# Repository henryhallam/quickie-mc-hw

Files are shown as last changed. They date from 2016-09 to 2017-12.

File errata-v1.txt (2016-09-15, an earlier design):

Molex SL footprint peg holes are wrong
R6 / R7 silkscreen swapped
dimm pegs could be tighter
D1 wrong pinout
SL != C-grid, don't have SL crimper
label phases on current sensors
Standoffs wrong height

Lower voltage filter pole ~300 Hz
Snubber across bus?

Protect 5V rail from transients on 15V

didn't order u1

Ifb very dirty in general, need to bring sensors closer, add diff amp, try using Rds(on)

When doing own gate drive board - ensure minimal capacitance across isolated power domains (particularly high side)

Vds feedback fails badly during regen (conduction through D2..4 and U3..5 clamping diodes),
possibly also responsible for some of the EMI.  Delete Vds FB or use series resistance to limit current flow.
Similarly, gate drive board doesn't provide desaturation protection during regeneration.

Hardware OVP would be nice

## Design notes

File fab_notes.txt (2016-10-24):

Fab notes for Kittyverter V2:

Tech contact: Henry Hallam henry@kittyhawk.aero

-----
Board fabrication notes:

6 layers FR-4
Board dimensions 5.34 x 4.78 inches
Finished thickness 92 mils +/- 10%
2 oz copper on outer layers, 7 mil trace / space
3 oz copper on inner layers, 9 mil trace / space
Dielectric thickness between layers 2-3, 3-4 and 4-5:
 4.5 mils min, 6.5 mils max
Dielectric thickness between layers 1-2, 5-6:
 Approx 27 mils, adjust as needed for finished thickness

J4, J5, J6, J8, J9, J11, J12 need plated, routed slots to fit
0.146 x 0.344 inch rectangular foot for component B6A-PCB:
https://lugsdirect.com/PDF_Webprint/B10-PCB,B6-PCB(-45),%20PCB-LAYOUT(web).pdf
A routing bit diameter 0.020" or smaller should be used.
See the F.Fab layer for a rectangular outline that can be used to
generate the tool path - the finished edge of the slot should be coincident
with that rectange.  0.020" drilled holes provide relief in the corners.
The 0.145" central drilled hole may be used to start the router cut, or
omitted.

I1, I2, I3 also need plated, routed slots; these are described by the "oval"
pad type in KiCad.  They are to fit the PFF leadform, see page 27 of
www.allegromicro.com/~/media/Files/Datasheets/ACS770-Datasheet.ashx

-----
Assembly notes:

B6A-PCB orderable from https://lugsdirect.com/B6A-PCB-HEX.htm or we can furnish.
I1, I2, I3, T1 should be installed on board underside.

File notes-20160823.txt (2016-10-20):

PSU: 60V 10A
RPM: 400
Torque ~1.15 Nm

HAL_PWM_DB*ED_CNT = 13:
Current ringing approx 2A pk-pk
phase-phase voltage @ motor ~180% of switch

HAL_PWM_DB*ED_CNT = 25:
similar

Smaller PWM series resistor?
Viper26 startup current through switch?
easy disconnect for HV->5V
footprint for LPF cap near current sensors

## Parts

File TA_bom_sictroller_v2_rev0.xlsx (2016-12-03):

Reference Designator | Quantity | Description/Value | Manufacturer Part Number (MPN)
C13,C10,C11,C12,C14,C15 | 6 | CAP CER 2.2uF 6.3V | GRM155C70J225KE11D
C131,C129,C128,C126,C117,C115,C114,C112,C103,C101,C100,C98,C48,C1,C24,C22,C21,C19,C17,C16,C60,C59,C58,C56,C55,C54,C53,C50,C40 | 29 | CAP CER 0.1uF 16V | GCM155R71C104KA55J
C132,C130,C118,C116,C104,C102 | 6 | DNA | DNA
C25,C23 | 2 | CAP CER 0.01uF 50V | GCM155R71H103KA55D
C37 | 1 | CAP CER 0.047uF 25V | GCM155R71E473KA55D
C38,C57,C51,C41 | 4 | CAP CER 2200pF 50V | GCM155R71H222KA37D
C49,C47,C45,C43 | 4 | CAP CER 470pF 100V | GCM155R72A471KA37D
C122,C120,C108,C106,C94,C92 | 6 | CAP CER 0.1uF 50V | GCJ188R71H104KA12D
C127,C125,C113,C111,C99,C97,C34,C39,C52 | 9 | CAP CER 1uF 35V | CGA3E1X7R1V105K080AE
C31,C29,C27 | 3 | CAP CER 10uF 10V | GRT188C81A106ME13D
C9,C8,C7,C6,C5,C4,C3,C2 | 8 | CAP CER 2.2uF 10V | C1608X7R1A225K080AE
C121,C119,C107,C105,C93,C91 | 6 | CAP CER 1uF 50V | GCJ21BR71H105KA01L
C124,C123,C110,C109,C96,C95,C20,C18,C30,C28,C26,C35 | 12 | CAP CER 10uF 16V | CGA4J1X7S1C106M125AE
C33 | 1 | CAP CER 470pF 1KV | GRM31B7U3A471JW31L
C46,C44,C42 | 3 | CAP PPS 0.1uF 16V | ECH-U1C104GX5
C62,C61 | 2 | CAP CER 0.047UF 1KV | C1210W473KDRACTU
C32 | 1 | CAP CER 0.47UF 1KV | 2220Y1K00474KXTWS2
C36 | 1 | CAP CER 100UF 16V | CKG57NX7S1C107M500JJ
C90,C89,C88,C87,C86,C85,C84,C83,C82,C81,C80,C79,C78,C77,C76,C75,C74,C73,C72,C71,C70,C69,C68,C67,C66,C65,C64,C63 | 28 | CAP CER 1uF 500V | B58031I5105M
D29,D25,D21,D17,D13,D9 | 6 | DIODE 1kV ULTRAFAST | US1M
D3,D2,D1 | 3 | TVS 3.3V DUAL | ESD7C3.3DT5G
D30,D26,D22,D18,D14,D10 | 6 | DIODE ZENER 4.3V | BZT585B4V3T
D31,D28,D23,D20,D15,D12 | 6 | DIODE ZENER 10V | BZT585B10T
D32,D27,D24,D19,D16,D11,D7 | 7 | DIODE SCHOTTKY SMALL SIGNAL | RB521S30T1G
D33 | 1 | LED RED | XZM2ACR53W-1
D34 | 1 | LED YELLOW | XZM2ACY53W-1
D4 | 1 | DIODE 1kV FAST | RS1M
D5 | 1 | DIODE SCHOTTKY 5A | PMEG3050EP
D6 | 1 | DIODE FAST SW | 1N4148WT-7
D8 | 1 | TVS 5V DUAL | ESD7C5.0DT5G
F1 | 1 | FUSE 0.75A | BK/PCC-3/4-R
FID1,FID2,FID3,FID4,FID5,FID6,FID7,FID8,FID9,FID10,FID11,FID12,FID13,FID14,FID15,FID16,FID17,FID18,FID19,FID20 | 20 | Fiducials | DNA
GNDVIA,GNDVIA,GNDVIA,GNDVIA,GNDVIA,REF**,REF**,GNDVIA | 8 | Stitching vias | DNA
I3,I2,I1 | 3 | SENS HALL-EFF 100A | ACS770LCB-100B-PFF-T
J10,J7,J1 | 3 | CONN PICOBLADE 2 | 53261-0271
J12,J11,J9,J8,J6,J5,J4 | 7 | WIRE LUG PCB IHI | B6A-PCB
J14 | 1 | CONN PICOBLADE 5 | 53261-0571
J15 | 1 | CONN PICOBLADE 3 | 53261-0371
J2 | 1 | CONN PICOBLADE 8 | 53261-0871
J3 | 1 | CONN 2x5 1.27mm | FTSH-105-01-L-DV-K
L1 | 1 | IND 10uH 380mA | CBMF1608T100K
MNT1,MNT2,MNT3,MNT4 | 4 | Mounting holes | DNA
Q1 | 1 | MOSFET N-CH 30V | CSD17483F4
Q2 | 1 | Power module | DNA
R60,R79,R76,R71,R68,R63 | 6 | RES 10R 2% 0.4W | CMA02040X1009GB300
R13,R12,R11,R1 | 4 | RES 4.7K 1% | ERJ-2RKF4701X
R44,R40,R26 | 3 | RES 1.8K 0.1% | ERA-2AEB182X
R47,R50 | 2 | RES 100K 1% | ERJ-2RKF1003X
R54,R10,R8,R7,R43,R42 | 6 | RES 10K 1% | ERJ-2RKF1002X
R5 | 1 | RES 169R 0.1% | ERA-2AEB1690X
R22,R3 | 2 | RES 16.9K 0.1% | ERA-2AEB1692X
R80,R78,R75,R74,R72,R70,R67,R66,R64,R62,R59,R58 | 12 | RES 1K 1% | ERJ-2RKF1001X
R48 | 1 | RES 2.7K 0.1% | ERA-2AEB272X
R15,R14 | 2 | RES 42.2K 0.1% | ERA-2AEB4222X
R46,R41,R31,R24 | 4 | RES 3.3K 0.1% | ERA-2AEB332X
R39,R38,R37,R36 | 4 | RES 3.6K 0.1% | ERA-2AEB362X
R6,R4,R49,R51 | 4 | RES 330R 0.1% | ERA-2AEB331X
R25,R2 | 2 | RES 33K 0.1% | ERA-2AEB333X
R45 | 1 | RES 56K 1% | ERJ-2RKF5602X
R17,R16 | 2 | RES 10.7K 0.1% | ERA-2AEB1072X
R23 | 1 | DNA | DNA
R18 | 1 | RES 22R 1% | ERJ-PA3F22R0V
R21 | 1 | FERRITE BEAD | BK2125HS102-T
R35,R34,R33,R32,R30,R29,R28,R27 | 8 | RES 300K 1% HV | ERJ-P06F3003V
R57,R56 | 2 | RES 1M 5% HV | ERJ-P06J105V
R61,R65,R69,R73,R77,R81 | 6 | RES 47K 5% | ERJ-6GEYJ473V
R9 | 1 | RES 120R 5% | ERJ-P06J121V
R20,R19 | 2 | RES 51K 5% HV | ERJ-P08J513V
REF**,REF**,REF**,REF**,REF**,REF** | 6 | Mounting holes | DNA
T1 | 1 | Transformer flyback | 7508110151
TH1,TH2 | 2 | Thermistor | NCP15XW153J03RC
TIE1 | 1 | Net tie | DNA
U1 | 1 | Optocoupler logic | ACPL-M61L
U10 | 1 | Dual inverter | 74LVC2G04GV
U11 | 1 | Level shifter 8-bit | TXS0108ERGYR
U19,U18,U16,U15,U13,U12 | 6 | Iso DC-DC | MGJ1D051905MPC
U2 | 1 | MCU DSP Piccolo Instaspin | TMS320F28069MPFPQ
U20,U17,U14 | 3 | Iso half bridge gate drive | 2ED020I12-F2
U3 | 1 | XCVR CAN ISO | ADM3053BRWZ
U5,U4 | 2 | REG LDO ADJ | TPS76201DBV
U6 | 1 | DC-DC micro step-down | XCL221B181ER
U7 | 1 | AC/DC converter 800V | VIPER26HD
U8 | 1 | Dual isolator | ADUM5241
U9 | 1 | 4ch thermistor interface | MAX6691
W3,W2,W20,W19,W17,W15,W14,W13,W12,W11,W10,W9,W5,W1,W23,W24,W4 | 17 | Test points | DNA
Y1 | 1 | RESONATOR 20 MHz | CSTCE20M0V13

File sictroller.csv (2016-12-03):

Title | SiCtroller
Revision | 1.0
Date | 2016-07-31
Generated | Tue 16 Aug 2016 05:07:08 PM PDT
Company | Pericynthion Heavy Industries
Comment 1
Comment 2
Comment 3
Comment 4
Total Parts | 120
Total Unique Parts | 45
Ref | Qty | Value | Footprint | SKU | Supplier
C1 | 1 | 10uF 50VCapacitors_SMD:C_1210
C3 | 1 | 22uF 16VCapacitors_SMD:C_1210
C4 | 1 | 100uF 16Vsictroller:C_6x5
C2 | 1 | 470nFCapacitors_SMD:C_0603
C6 C5 | 2 | 10uFCapacitors_SMD:C_1210
C10 | 1 | 100 nF C0G 1%Capacitors_SMD:C_1210 | PCF1189CT-ND
C11 C15 C16 | 3 | 100 nF C0G 1%Capacitors_SMD:C_1210
C14 C20 C22 C23 C24 C8 C7 C13 C12 C19 C18 | 11 | DNPCapacitors_SMD:C_0603
C9 C17 C21 C26 C25 C27 | 6 | 1uFCapacitors_SMD:C_0603
C31 C28 C29 C30 C32 C36 C35 C34 C33 | 9 | 470pFCapacitors_SMD:C_0603
D1 | 1 | D_Schottky_x2_KCom_AKATO_SOT_Packages_SMD:SOT-323 | 497-5550-1-ND | Digikey
D2 | 1 | RS1MSWFQDiodes_SMD:SOD-123 | 745C101103JPCT-ND
D3 D4 | 2 | RS1MSWFQDiodes_SMD:SOD-123
D5 | 1 | BZT52B6V8Diodes_SMD:SOD-123
J4 J8 J9 J10 J11 | 5 | CONN_01X03sictroller:Molex-SL-3POS-RA
J1 | 1 | CONN_01X08Connectors_Molex:Connector_Molex_PicoBlade_53261-0871
J2 | 1 | CONN_01X12Connectors_Molex:Connector_Molex_PicoBlade_53261-1271
J3 | 1 | TMDSCNCD28069sictroller:5390213-1
J5 | 1 | BARREL_JACKsictroller:PJ-102B | CP-102B-ND
J7 | 1 | CONN_01X02sictroller:Molex-SL-2POS-RA
J6 | 1 | MICROFIT-10Connectors_Molex:Connector_Microfit3_Header_02x05_Angled_43045-100x
J12 | 1 | CONN_02X13Connect:IDC_Header_Straight_26pins
Q1 | 1 | FDG1024NZTO_SOT_Packages_SMD:SC-70-6
R1 | 1 | 9.1R 2WResistors_ThroughHole:Resistor_Horizontal_RM15mm
R2 | 1 | 0R/BEADResistors_SMD:R_0603
R8 | 1 | 150K 1% 250V 0.5WResistors_SMD:R_0805 | 667-ERJ-P06F1503V | Mouser
R9 R11 R12 R17 R18 R20 R21 | 7 | 150K 1% 250V 0.5WResistors_SMD:R_0805
R10 R13 R19 R22 | 4 | 1.8K 1%Resistors_SMD:R_0603
R14 R15 | 2 | DNPResistors_SMD:R_0603
R26 R28 R32 R35 R6 R23 R30 | 7 | 1.8KResistors_SMD:R_0603
R27 R29 R33 R36 R7 R24 R31 | 7 | 3.3KResistors_SMD:R_0603
R5 | 1 | 2.2KResistors_SMD:R_0603
R4 R16 R25 | 3 | 1kResistors_SMD:R_0603
R3 | 1 | 0RResistors_SMD:R_0603
R34 | 1 | 750Resistors_SMD:R_0603
R38 | 1 | 10kResistors_SMD:R_0603
R39 | 1 | 5k1Resistors_SMD:R_0603
R37 | 1 | 745C101103 (10k)Resistors_SMD:R_Array_Convex_5x1206 | 745C101103JPCT-ND
U2 | 1 | APE8865N-33-HF-3TO_SOT_Packages_SMD:SOT-23
U1 | 1 | V7805-500-SMTsictroller:V78-500-SMT | 490-V7805-500-SMT-TR | Mouser
U3 U4 U5 | 3 | MAX4195SMD_Packages:SOIC-8-N
U6 | 1 | 74LVC8T245Housings_SSOP:TSSOP-24_4.4x7.8mm_Pitch0.65mm
U7 | 1 | 74LVC2G04TO_SOT_Packages_SMD:TSOT-6-MK06A
W3 W4 W5 W6 W18 W20 W7 W8 W9 | 9 | TEST_1PMeasurement_Points:Measurement_Point_Round-TH_Small
W22 W19 W21 W23 W12 W15 W10 W13 W16 W2 W1 | 11 | TEST_1PMeasurement_Points:Measurement_Point_Round-SMD-Pad_Small
BOM made with KICAD_BOM_WIZARD (https://github.com/HashDefineElectronics/KiCad_BOM_Wizard.git)
Generated Tue 16 Aug 2016 05:07:08 PM PDT

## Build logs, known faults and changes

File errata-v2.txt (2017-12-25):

** V2.0 bringup notes and errata: **

~PWR_RESET pulldown R54 insufficient - system will attempt to turn on all switches at powerup. 
Replace with 1k and have software ensure PWM outputs are low before raising ~PWR_RESET.

Fault LED indicates not-fault.

VIPER26 aux supply unstable.  Add 1K resistor in series with D6.

D5 reverse voltage rating marginal.  Replace with PMEG6045 or similar.

Tempo populated D34 backwards on some boards

Above issues fixed in V2.1.

Add polyfuse in series with +5VD output to thrust ctrl lever to prevent short in that harness from taking down board.
Something dies horribly when system tries to spin motor with HV only connected through precharge resistor.
Add TVS on 5V rail
Larger vias for 5V supplies to gate drive? (320 mA).  Also from Viper.  Actually maybe they're fine.
Convenient connector for 5V.
Better voltage reference?
Precision resistor for R48
Just delete the 22R resistor, inductor and fuse between HV and Viper input.
Shield the cable to the Emrax thermistor
tRST should have pull-down not pull-up to boot standalone

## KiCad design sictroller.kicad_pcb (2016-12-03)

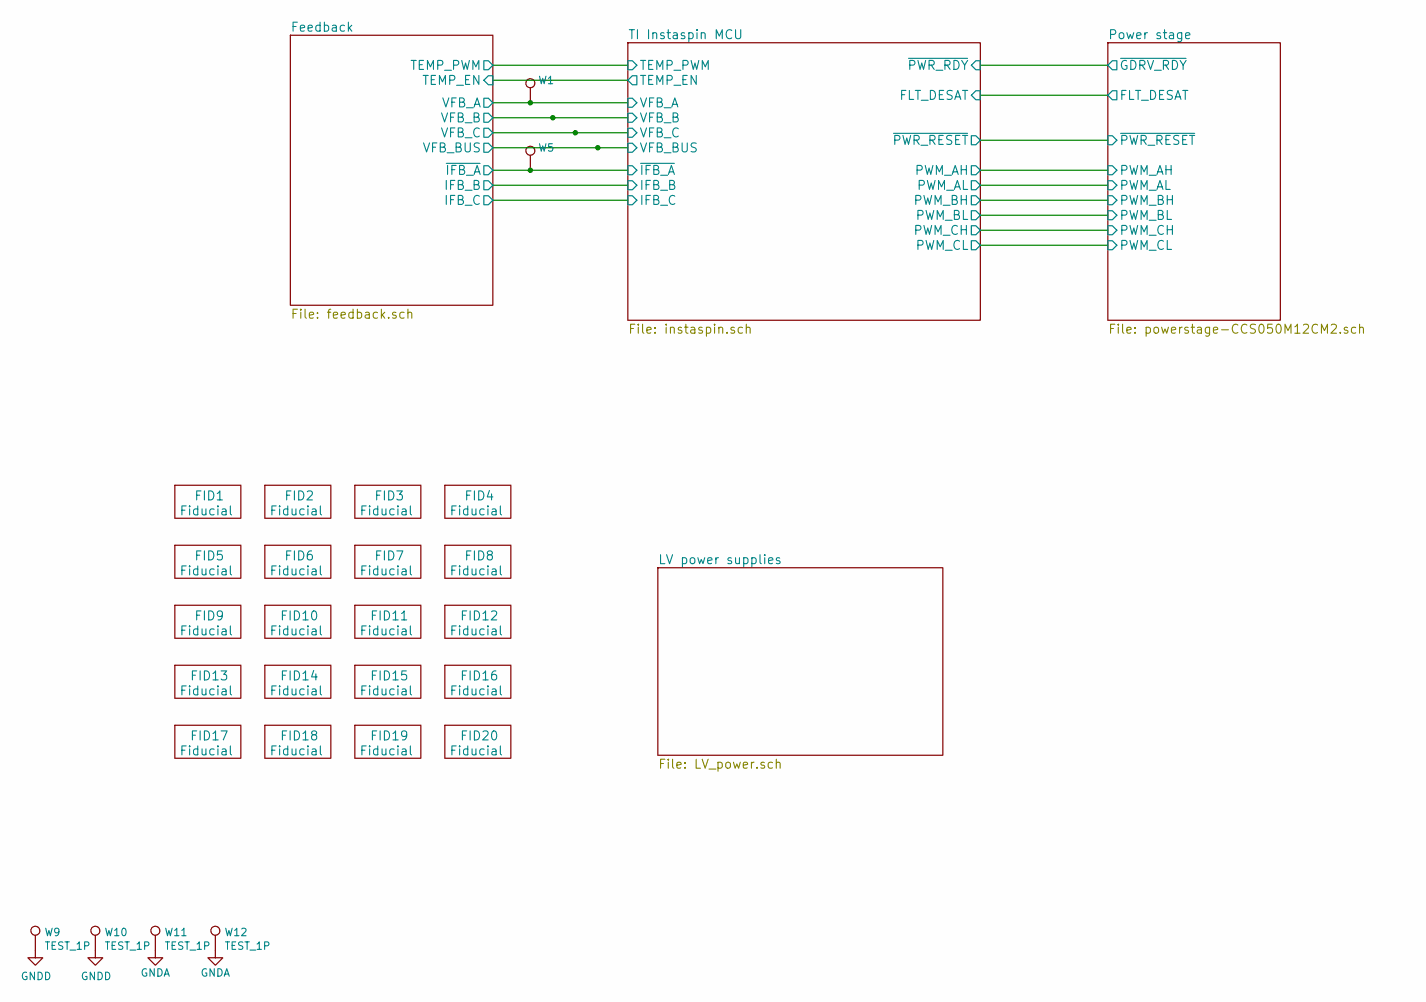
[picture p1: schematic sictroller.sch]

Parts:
FID1, FID2, FID3, FID4, FID5, FID6, FID7, FID8, FID9, FID10, FID11, FID12, FID13, FID14, FID15, FID16, FID17, FID18, FID19, FID20: Fiducial; Fiducial_1mm_CopperTop
W1, W5, W9, W10, W11, W12: TEST_1P; Measurement_Point_Round-TH_Small

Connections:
/Feedback/VFB_A: W1.1; also elsewhere on the board
/Feedback/~IFB_A: W5.1; also elsewhere on the board
GND: W9.1, W10.1; also elsewhere on the board
GNDA: W11.1, W12.1; also elsewhere on the board

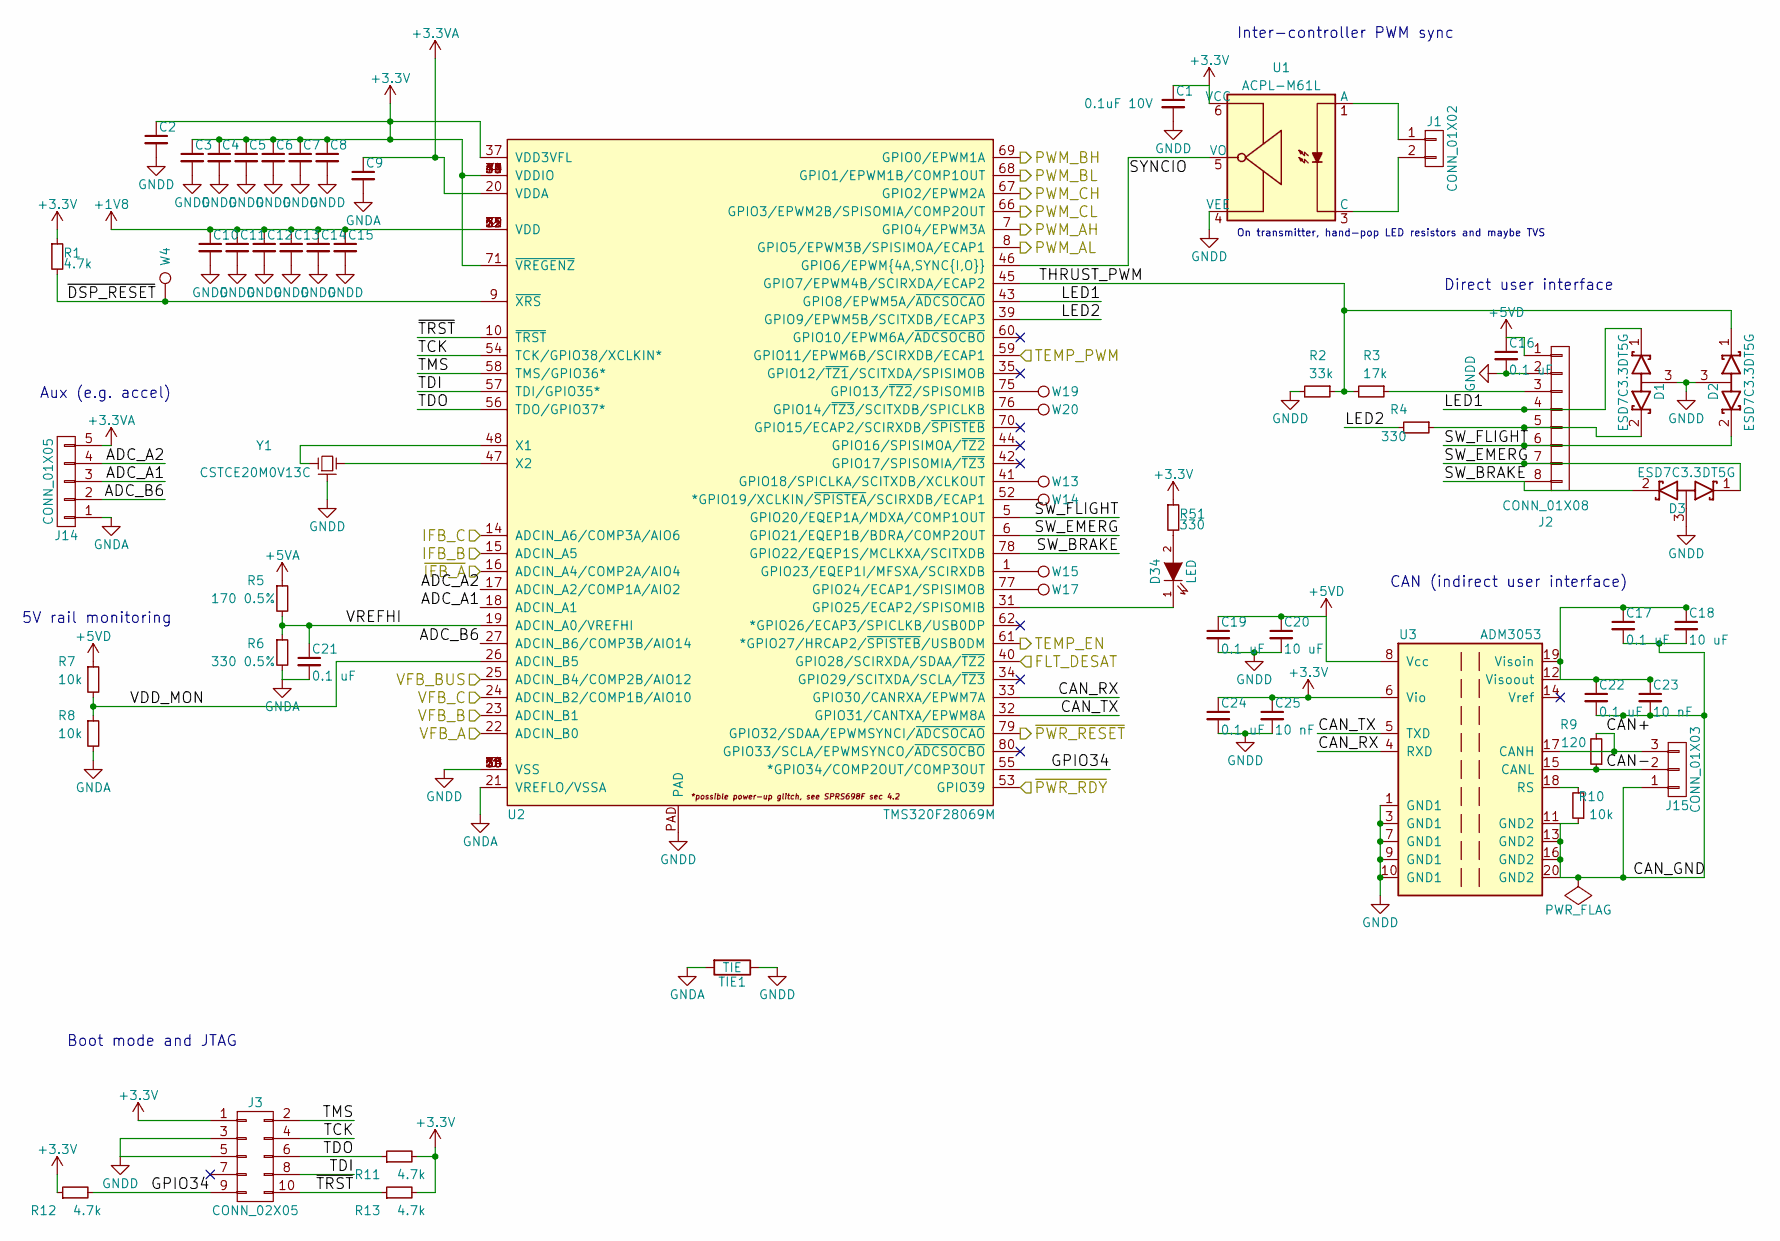
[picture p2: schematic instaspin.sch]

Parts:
C1: 0.1uF 10V; C_0402
C2, C3, C4, C5, C6, C7, C8, C9: 2.2uF 10V; C_0603
C10, C11, C12, C13, C14, C15: 2.2uF 6V; C_0402
C16, C17, C19, C21, C22, C24: 0.1 uF; C_0402
C18, C20: 10 uF; C_0805
C23, C25: 10 nF; C_0402
D1, D2, D3: ESD7C3.3DT5G; SOT-723
D34: LED; LED_0603
J1: CONN_01X02; Molex_PicoBlade_53261-0271
J2: CONN_01X08; Molex_PicoBlade_53261-0871
J3: CONN_02X05; FTSH-105-01-L-DV-K
J14: CONN_01X05; Molex_PicoBlade_53261-0571
J15: CONN_01X03; Molex_PicoBlade_53261-0371
R1, R11, R12, R13: 4.7k; R_0402
R2: 33k; R_0402
R3: 17k; R_0402
R4, R51: 330; R_0402
R5: 170 0.5%; R_0402
R6: 330 0.5%; R_0402
R7, R8, R10: 10k; R_0402
R9: 120; R_0805
TIE1: TIE; NetTie-_Connected_Small
U1: ACPL-M61L; ACPL-M61L_SO-5
U2: TMS320F28069M; PFP
U3: ADM3053; SOIC-20W_7.5x12.8mm_Pitch1.27mm
W4, W13, W14, W15, W17, W19, W20: TEST_1P; Measurement_Point_Round-TH_Small
Y1: CSTCE20M0V13C; CSTCE_V13C

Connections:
+1V8: C10.1, C11.1, C12.1, C13.1, C14.1, C15.1, U2.2 (VDD), U2.12 (VDD), U2.29 (VDD), U2.51 (VDD), U2.65 (VDD), U2.72 (VDD); also elsewhere on the board
+3.3VA: C9.1, J14.5, U2.20 (VDDA); also elsewhere on the board
+3V3: C1.1, C2.1, C3.1, C4.1, C5.1, C6.1, C7.1, C8.1, C24.1, C25.1, J3.1, R1.1, R11.2, R12.1, R13.2, R51.1, U1.6 (VCC), U2.4 (VDDIO), U2.11 (VDDIO), U2.30 (VDDIO), U2.37 (VDD3VFL), U2.49 (VDDIO), U2.63 (VDDIO), U2.71 (~VREGENZ), U2.74 (VDDIO), U3.6 (Vio); also elsewhere on the board
+5VA: R5.1; also elsewhere on the board
+5VD: C16.1, C19.1, C20.1, J2.1, R7.1, U3.8 (Vcc); also elsewhere on the board
/Feedback/IFB_B: U2.15 (ADCIN_A5); also elsewhere on the board
/Feedback/IFB_C: U2.14 (ADCIN_A6/COMP3A/AIO6); also elsewhere on the board
/Feedback/TEMP_EN: U2.61 (*GPIO27/HRCAP2/~SPISTEB~/USB0DM); also elsewhere on the board
/Feedback/TEMP_PWM: U2.59 (GPIO11/EPWM6B/SCIRXDB/ECAP1); also elsewhere on the board
/Feedback/VFB_A: U2.22 (ADCIN_B0); also elsewhere on the board
/Feedback/VFB_B: U2.23 (ADCIN_B1); also elsewhere on the board
/Feedback/VFB_BUS: U2.25 (ADCIN_B4/COMP2B/AIO12); also elsewhere on the board
/Feedback/VFB_C: U2.24 (ADCIN_B2/COMP1B/AIO10); also elsewhere on the board
/Feedback/~IFB_A: U2.16 (ADCIN_A4/COMP2A/AIO4); also elsewhere on the board
/Power stage/FLT_DESAT: U2.40 (GPIO28/SCIRXDA/SDAA/~TZ2); also elsewhere on the board
/Power stage/PWM_AH: U2.7 (GPIO4/EPWM3A); also elsewhere on the board
/Power stage/PWM_AL: U2.8 (GPIO5/EPWM3B/SPISIMOA/ECAP1); also elsewhere on the board
/Power stage/PWM_BH: U2.69 (GPIO0/EPWM1A); also elsewhere on the board
/Power stage/PWM_BL: U2.68 (GPIO1/EPWM1B/COMP1OUT); also elsewhere on the board
/Power stage/PWM_CH: U2.67 (GPIO2/EPWM2A); also elsewhere on the board
/Power stage/PWM_CL: U2.66 (GPIO3/EPWM2B/SPISOMIA/COMP2OUT); also elsewhere on the board
/Power stage/~GDRV_RDY: U2.53 (GPIO39); also elsewhere on the board
/Power stage/~PWR_RESET: U2.79 (GPIO32/SDAA/EPWMSYNCI/~ADCSOCAO); also elsewhere on the board
/TI Instaspin MCU/ADC_A1: J14.3, U2.18 (ADCIN_A1)
/TI Instaspin MCU/ADC_A2: J14.4, U2.17 (ADCIN_A2/COMP1A/AIO2)
/TI Instaspin MCU/ADC_B6: J14.2, U2.27 (ADCIN_B6/COMP3B/AIO14)
/TI Instaspin MCU/CAN+: J15.3, R9.2, U3.17 (CANH)
/TI Instaspin MCU/CAN-: J15.2, R9.1, U3.15 (CANL)
/TI Instaspin MCU/CAN_GND: C17.2, C18.2, C22.2, C23.2, J15.1, R10.1, U3.11 (GND2), U3.13 (GND2), U3.16 (GND2), U3.20 (GND2)
/TI Instaspin MCU/CAN_RX: U2.33 (GPIO30/CANRXA/EPWM7A), U3.4 (RXD)
/TI Instaspin MCU/CAN_TX: U2.32 (GPIO31/CANTXA/EPWM8A), U3.5 (TXD)
/TI Instaspin MCU/GPIO34: J3.9, R12.2, U2.55 (*GPIO34/COMP2OUT/COMP3OUT)
/TI Instaspin MCU/LED1: D1.1 (K), J2.4, U2.43 (GPIO8/EPWM5A/~ADCSOCAO)
/TI Instaspin MCU/LED2: R4.2, U2.39 (GPIO9/EPWM5B/SCITXDB/ECAP3)
/TI Instaspin MCU/SW_BRAKE: D3.2 (K), J2.8, U2.78 (GPIO22/EQEP1S/MCLKXA/SCITXDB)
/TI Instaspin MCU/SW_EMERG: D3.1 (K), J2.7, U2.6 (GPIO21/EQEP1B/BDRA/COMP2OUT)
/TI Instaspin MCU/SW_FLIGHT: D2.2 (K), J2.6, U2.5 (GPIO20/EQEP1A/MDXA/COMP1OUT)
/TI Instaspin MCU/SYNCIO: U1.5 (VO), U2.46 (GPIO6/EPWM{4A,SYNC{I,O}})
/TI Instaspin MCU/TCK: J3.4, U2.54 (TCK/GPIO38/XCLKIN*)
/TI Instaspin MCU/TDI: J3.8, U2.57 (TDI/GPIO35*)
/TI Instaspin MCU/TDO: J3.6, R11.1, U2.56 (TDO/GPIO37*)
/TI Instaspin MCU/THRUST_PWM: D2.1 (K), R2.1, R3.2, U2.45 (GPIO7/EPWM4B/SCIRXDA/ECAP2)
/TI Instaspin MCU/TMS: J3.2, U2.58 (TMS/GPIO36*)
/TI Instaspin MCU/VDD_MON: R7.2, R8.1, U2.26 (ADCIN_B5)
/TI Instaspin MCU/VREFHI: C21.1, R5.2, R6.1, U2.19 (ADCIN_A0/VREFHI)
/TI Instaspin MCU/~DSP_RESET: R1.2, U2.9 (~XRS), W4.1
/TI Instaspin MCU/~TRST: J3.10, R13.1, U2.10 (~TRST)
GND: C1.2, C2.2, C3.2, C4.2, C5.2, C6.2, C7.2, C8.2, C10.2, C11.2, C12.2, C13.2, C14.2, C15.2, C16.2, C19.2, C20.2, C24.2, C25.2, D1.3 (A), D2.3 (A), D3.3 (A), J2.2, J3.3, J3.5, R2.2, TIE1.1, U1.4 (VEE), U2.3 (VSS), U2.13 (VSS), U2.28 (VSS), U2.38 (VSS), U2.50 (VSS), U2.64 (VSS), U2.73 (VSS), U2.PAD, U3.1 (GND1), U3.3 (GND1), U3.7 (GND1), U3.9 (GND1), U3.10 (GND1), Y1.2 (common); also elsewhere on the board
GNDA: C9.2, C21.2, J14.1, R6.2, R8.2, TIE1.2, U2.21 (VREFLO/VSSA); also elsewhere on the board
unnamed: C17.1, C18.1, C22.1, C23.1, U3.12 (Visoout), U3.19 (Visoin)
unnamed: D1.2 (K), J2.5, R4.1
unnamed: D34.1 (K), U2.31 (GPIO25/ECAP2/SPISOMIB)
unnamed: D34.2 (A), R51.2
unnamed: J1.1, U1.1 (A)
unnamed: J1.2, U1.3 (C)
unnamed: J2.3, R3.1
unnamed: R10.2, U3.18 (RS)
unnamed: U2.1 (GPIO23/EQEP1I/MFSXA/SCIRXDB), W15.1
unnamed: U2.41 (GPIO18/SPICLKA/SCITXDB/XCLKOUT), W13.1
unnamed: U2.47 (X2), Y1.3 (2)
unnamed: U2.48 (X1), Y1.1
unnamed: U2.52 (*GPIO19/XCLKIN/~SPISTEA~/SCIRXDB/ECAP1), W14.1
unnamed: U2.75 (GPIO13/~TZ2~/SPISOMIB), W19.1
unnamed: U2.76 (GPIO14/~TZ3~/SCITXDB/SPICLKB), W20.1
unnamed: U2.77 (GPIO24/ECAP1/SPISIMOB), W17.1

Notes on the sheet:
Boot mode and JTAG
On transmitter, hand-pop LED resistors and maybe TVS
Inter-controller PWM sync
Direct user interface
CAN (indirect user interface)
5V rail monitoring
Aux (e.g. accel)

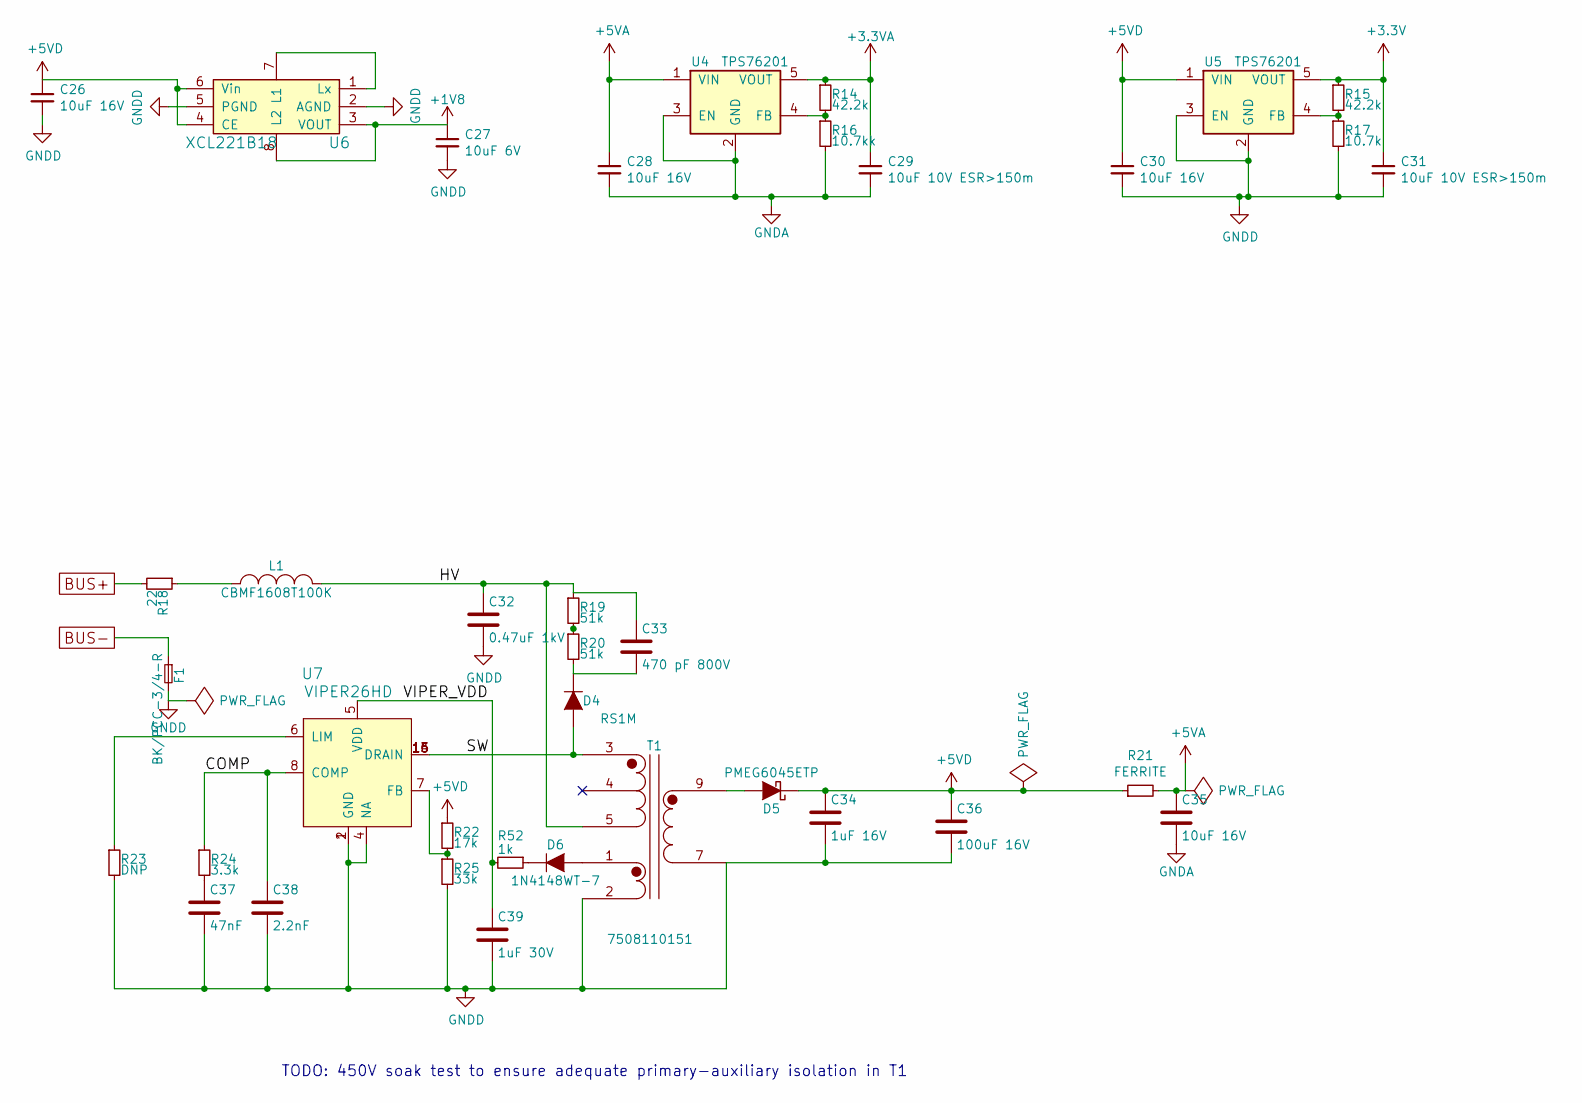
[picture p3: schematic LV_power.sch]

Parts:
C26, C28, C30, C35: 10uF 16V; C_0805
C27: 10uF 6V; C_0603
C29, C31: 10uF 10V ESR>150m; C_0603
C32: 0.47uF 1kV; C_2220
C33: 470 pF 800V; C_1206
C34: 1uF 16V; C_0603
C36: 100uF 16V; C_6x5
C37: 47nF; C_0402
C38: 2.2nF; C_0402
C39: 1uF 30V; C_0603
D4: RS1M; SMA_Standard
D5: PMEG6045ETP; SOD-128
D6: 1N4148WT-7; SOD-523
F1: BK/PCC-3/4-R; Fuse_TE5_Littlefuse-395Series
L1: CBMF1608T100K; R_0603
R14, R15: 42.2k; R_0402
R16: 10.7kk; R_0402
R17: 10.7k; R_0402
R18: 22; R_0603
R19, R20: 51k; R_1206
R21: FERRITE; R_0805
R22: 17k; R_0402
R23: DNP; R_0402
R24: 3.3k; R_0402
R25: 33k; R_0402
R52: 1k; R_0402
T1: 7508110151; WE-7508110151
U4, U5: TPS76201; SOT-23-5
U6: XCL221B18; XCL22x
U7: VIPER26HD; SOIC-16_3.9x9.9mm_Pitch1.27mm

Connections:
+1V8: C27.1, U6.3 (VOUT), U6.8 (L2); also elsewhere on the board
+3.3VA: C29.1, R14.1, U4.5 (VOUT); also elsewhere on the board
+3V3: C31.1, R15.1, U5.5 (VOUT); also elsewhere on the board
+5VA: C28.1, C35.1, R21.2, U4.1 (VIN); also elsewhere on the board
+5VD: C26.1, C30.1, C34.1, C36.1, D5.1 (K), R21.1, R22.1, U5.1 (VIN), U6.4 (CE), U6.6 (Vin); also elsewhere on the board
/LV power supplies/COMP: C38.1, R24.1, U7.8 (COMP)
/LV power supplies/HV: C32.1, C33.1, L1.2, R19.1, T1.5 (PR2)
/LV power supplies/SW: D4.2 (A), T1.3 (PR1), U7.13 (DRAIN), U7.14 (DRAIN), U7.15 (DRAIN), U7.16 (DRAIN)
/LV power supplies/VIPER_VDD: C39.1, R52.2, U7.5 (VDD)
BUS+: R18.2; also elsewhere on the board
BUS-: F1.1; also elsewhere on the board
GND: C26.2, C27.2, C30.2, C31.2, C32.2, C34.2, C36.2, C37.2, C38.2, C39.2, F1.2, R17.2, R23.2, R25.2, T1.2 (AUX2), T1.7 (S1), U5.2 (GND), U5.3 (EN), U6.2 (AGND), U6.5 (PGND), U7.1 (GND), U7.2 (GND), U7.4 (NA); also elsewhere on the board
GNDA: C28.2, C29.2, C35.2, R16.2, U4.2 (GND), U4.3 (EN); also elsewhere on the board
unnamed: C33.2, D4.1 (K), R20.2
unnamed: C37.1, R24.2
unnamed: D5.2 (A), T1.9 (S2)
unnamed: D6.1 (K), R52.1
unnamed: D6.2 (A), T1.1 (AUX1)
unnamed: L1.1, R18.1
unnamed: R14.2, R16.1, U4.4 (FB)
unnamed: R15.2, R17.1, U5.4 (FB)
unnamed: R19.2, R20.1
unnamed: R22.2, R25.1, U7.7 (FB)
unnamed: R23.1, U7.6 (LIM)
unnamed: U6.1 (Lx), U6.7 (L1)

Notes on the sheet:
TODO: 450V soak test to ensure adequate primary-auxiliary isolation in T1

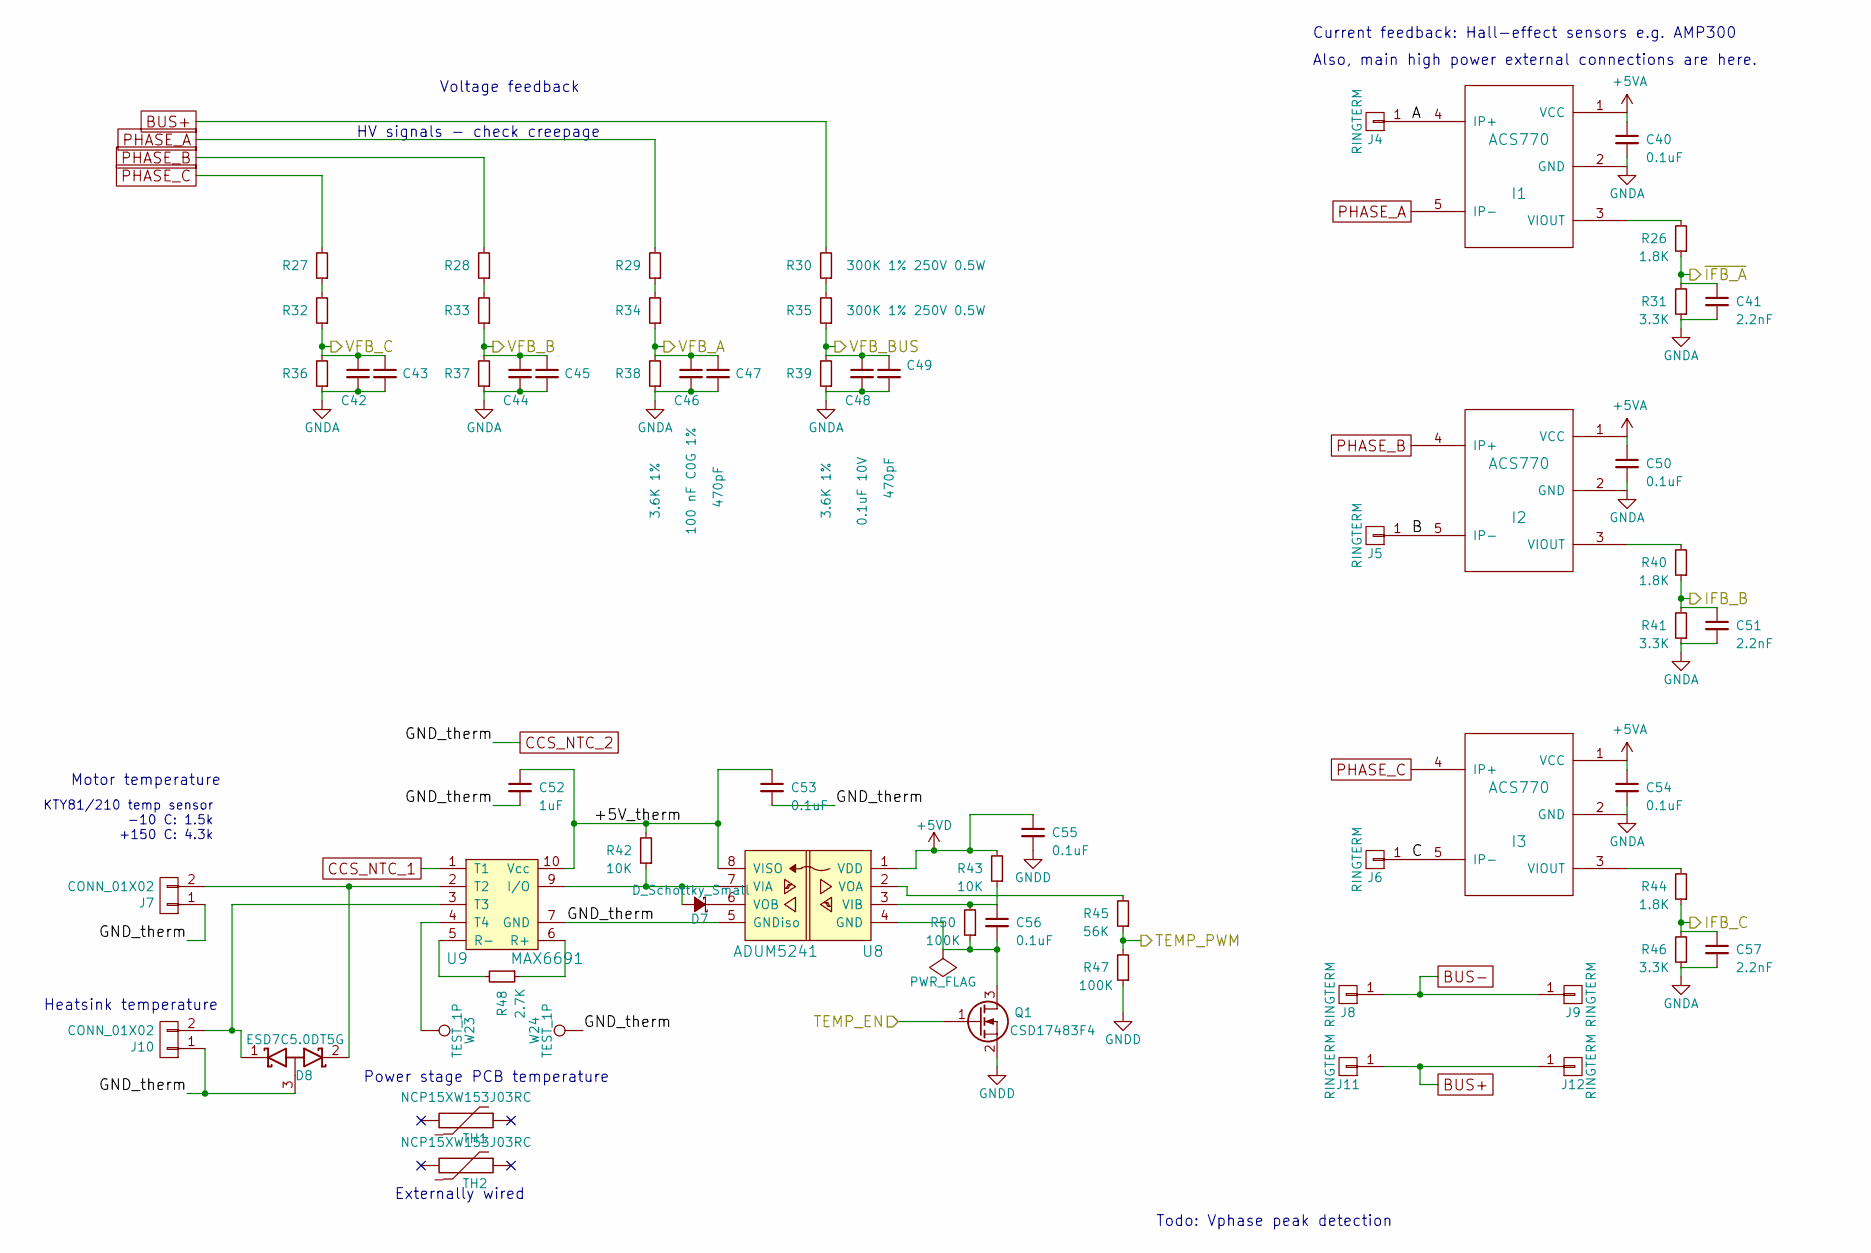
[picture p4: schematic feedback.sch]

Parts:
C40, C50, C53, C54, C55, C56: 0.1uF; C_0402
C41, C51, C57: 2.2nF; C_0402
C42, C44, C46: 100 nF C0G 1%; C_1210
C43, C45, C47, C49: 470pF; C_0402
C48: 0.1uF 10V; C_0402
C52: 1uF; C_0603
D7: D_Schottky_Small; SOD-523
D8: ESD7C5.0DT5G; SOT-723
I1, I2, I3: ACS770
J4, J5, J6, J8, J9, J11, J12: RINGTERM; B6A-PCB
J7, J10: CONN_01X02; Molex_PicoBlade_53261-0271
Q1: CSD17483F4; FEMTOFET_YJC_YJJ
R26, R40, R44: 1.8K; R_0402
R27, R28, R29, R30, R32, R33, R34, R35: 300K 1% 250V 0.5W; R_0805
R31, R41, R46: 3.3K; R_0402
R36, R37, R38, R39: 3.6K 1%; R_0402
R42, R43: 10K; R_0402
R45: 56K; R_0402
R47, R50: 100K; R_0402
R48: 2.7K; R_0402
TH1, TH2: NCP15XW153J03RC; R_0402_extwire
U8: ADUM5241; SOIC-8_3.9x4.9mm_Pitch1.27mm
U9: MAX6691; MSOP-10_3x3mm_Pitch0.5mm
W23, W24: TEST_1P; Measurement_Point_Round-TH_Small

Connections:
+5VA: C40.1, C50.1, C54.1, I1.1 (VCC), I2.1 (VCC), I3.1 (VCC); also elsewhere on the board
+5VD: C55.1, R43.2, U8.1 (VDD); also elsewhere on the board
/Feedback/+5V_therm: C52.1, C53.1, R42.2, U8.8 (VISO), U9.10 (Vcc)
/Feedback/A: I1.4 (IP+), J4.1
/Feedback/B: I2.5 (IP-), J5.1
/Feedback/C: I3.5 (IP-), J6.1
/Feedback/IFB_B: C51.1, R40.1, R41.2; also elsewhere on the board
/Feedback/IFB_C: C57.1, R44.1, R46.2; also elsewhere on the board
/Feedback/TEMP_EN: Q1.1 (G); also elsewhere on the board
/Feedback/TEMP_PWM: R45.1, R47.2; also elsewhere on the board
/Feedback/VFB_A: C46.1, C47.1, R34.1, R38.2; also elsewhere on the board
/Feedback/VFB_B: C44.1, C45.1, R33.1, R37.2; also elsewhere on the board
/Feedback/VFB_BUS: C48.1, C49.1, R35.1, R39.2; also elsewhere on the board
/Feedback/VFB_C: C42.1, C43.1, R32.1, R36.2; also elsewhere on the board
/Feedback/~IFB_A: C41.1, R26.1, R31.2; also elsewhere on the board
BUS+: J11.1, J12.1, R30.2; also elsewhere on the board
BUS-: J8.1, J9.1; also elsewhere on the board
CCS_NTC_1: U9.1 (T1); also elsewhere on the board
CCS_NTC_2: C52.2, C53.2, D8.3 (A), J7.1, J10.1, U8.5 (GNDiso), U9.7 (GND), W24.1; also elsewhere on the board
GND: C55.2, Q1.2 (S), R47.1; also elsewhere on the board
GNDA: C40.2, C41.2, C42.2, C43.2, C44.2, C45.2, C46.2, C47.2, C48.2, C49.2, C50.2, C51.2, C54.2, C57.2, I1.2 (GND), I2.2 (GND), I3.2 (GND), R31.1, R36.1, R37.1, R38.1, R39.1, R41.1, R46.1; also elsewhere on the board
unnamed: C56.1, R43.1, R50.2, U8.3 (VIB)
unnamed: C56.2, Q1.3 (D), R50.1, U8.4 (GND)
unnamed: D7.1 (K), U8.6 (VOB)
unnamed: D7.2 (A), R42.1, U8.7 (VIA), U9.9 (I/O)
unnamed: D8.1 (K), J10.2, U9.3 (T3)
unnamed: D8.2 (K), J7.2, U9.2 (T2)
unnamed: I1.3 (VIOUT), R26.2
unnamed: I2.3 (VIOUT), R40.2
unnamed: I3.3 (VIOUT), R44.2
unnamed: R27.1, R32.2
unnamed: R28.1, R33.2
unnamed: R29.1, R34.2
unnamed: R30.1, R35.2
unnamed: R45.2, U8.2 (VOA)
unnamed: R48.1, U9.6 (R+)
unnamed: R48.2, U9.5 (R-)
unnamed: U9.4 (T4), W23.1
PHASE_A: I1.5 (IP-), R29.2; also elsewhere on the board
PHASE_B: I2.4 (IP+), R28.2; also elsewhere on the board
PHASE_C: I3.4 (IP+), R27.2; also elsewhere on the board

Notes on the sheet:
HV signals - check creepage
Todo: Vphase peak detection
KTY81/210 temp sensor -10 C: 1.5k +150 C: 4.3k
Current feedback: Hall-effect sensors e.g. AMP300
Voltage feedback
Motor temperature
Heatsink temperature
Power stage PCB temperature
Also, main high power external connections are here.
Externally wired

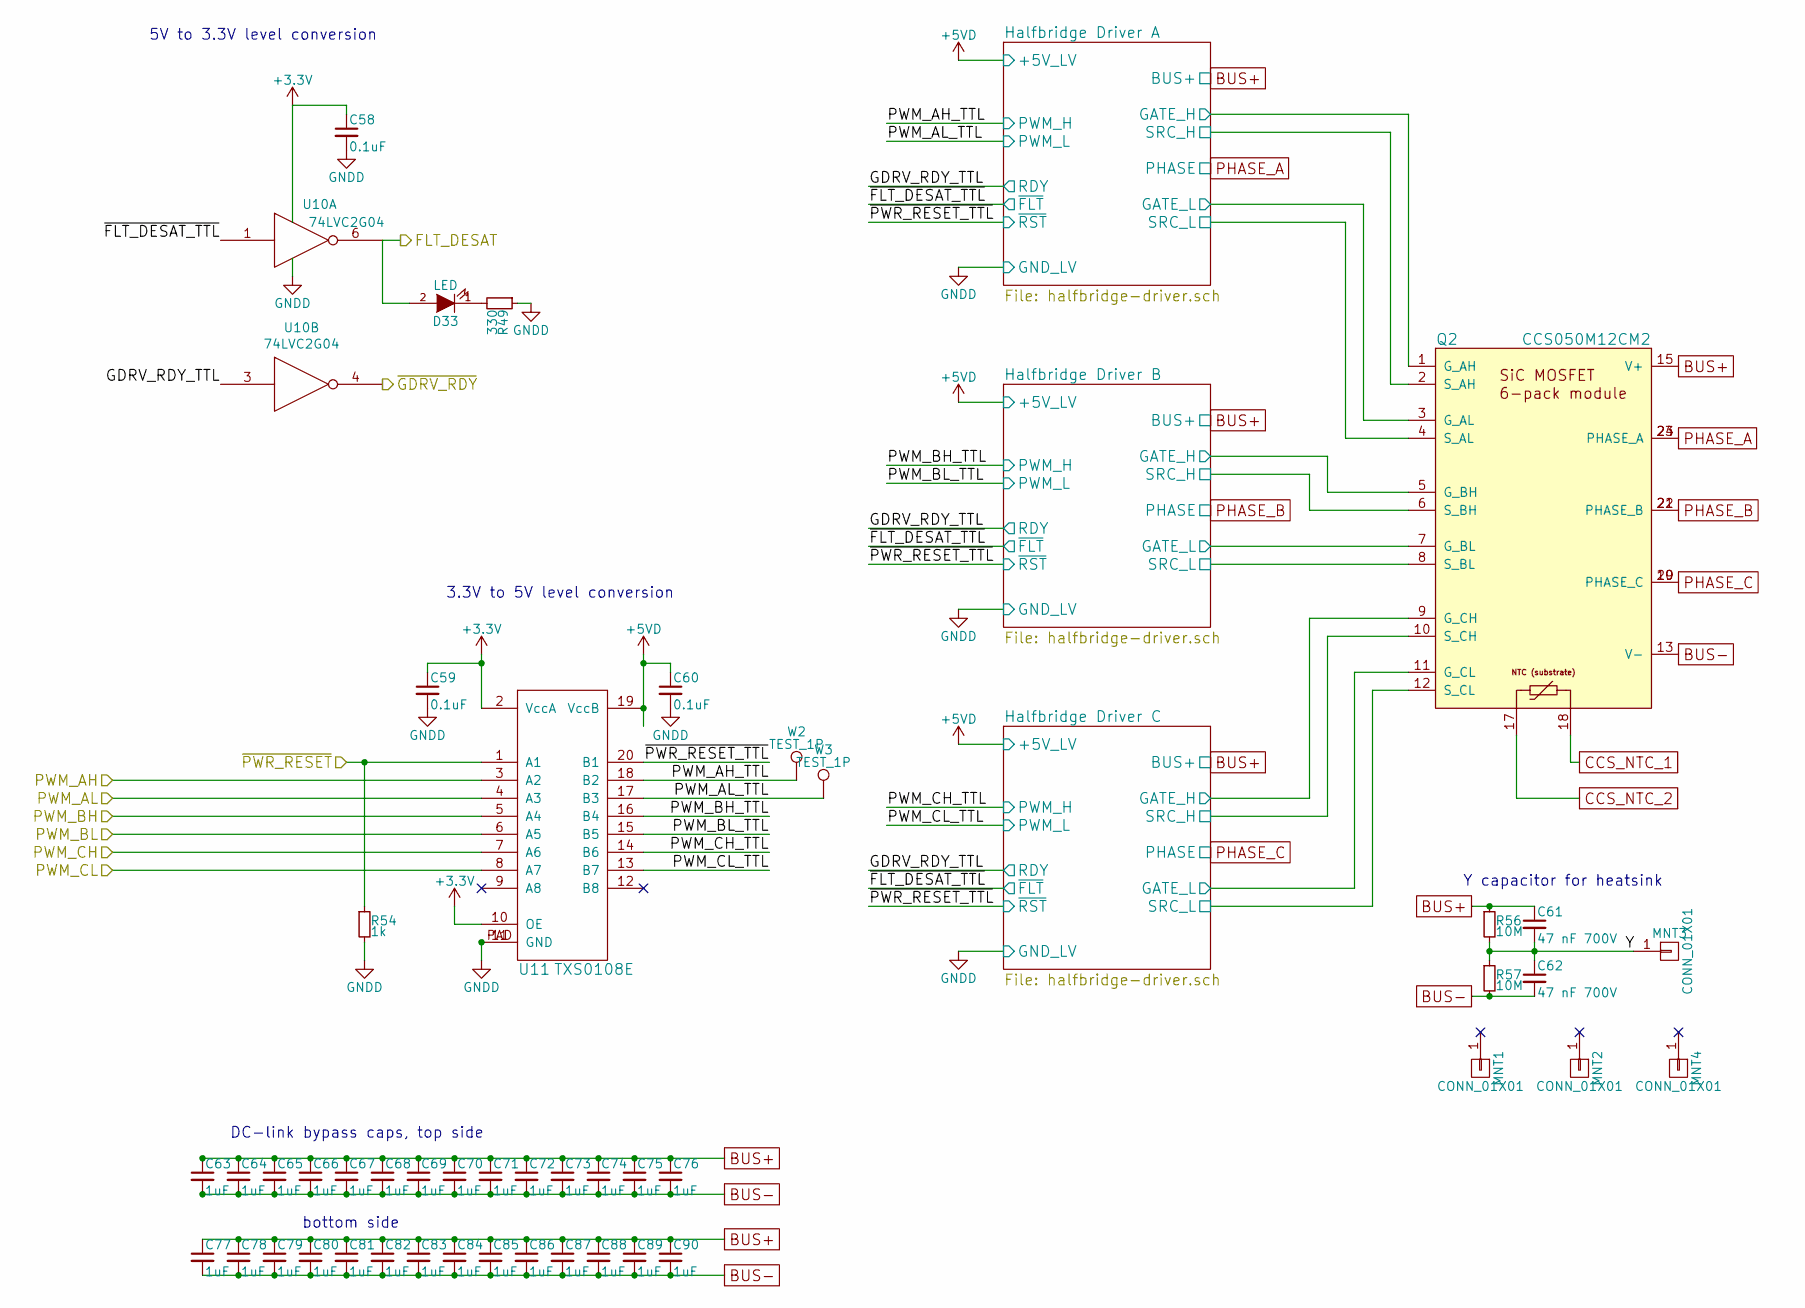
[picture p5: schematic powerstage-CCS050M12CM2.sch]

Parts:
C58, C59, C60: 0.1uF; C_0402
C61, C62: 47 nF 700V; C_1210
C63, C64, C65, C66, C67, C68, C69, C70, C71, C72, C73, C74, C75, C76: 1uF; Ceralink-L-viastitch
C77, C78, C79, C80, C81, C82, C83, C84, C85, C86, C87, C88, C89, C90: 1uF; Ceralink-L
D33: LED; LED_0603
MNT1, MNT2, MNT3, MNT4: CONN_01X01; MountingHole_3mm_Pad_Via
Q2: CCS050M12CM2; 6pack-45mm
R49: 330; R_0402
R54: 1k; R_0402
R56, R57: 10M; R_0805
U10: 74LVC2G04; TSOT-6-MK06A
U11: TXS0108E; VQFN-20
W2, W3: TEST_1P; Measurement_Point_Round-TH_Small

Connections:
+3V3: C58.1, C59.1, U10.5 (VCC), U11.2 (VccA), U11.10 (OE); also elsewhere on the board
+5VD: C60.1, U11.19 (VccB); also elsewhere on the board
/Power stage/FLT_DESAT: D33.2 (A), U10.6; also elsewhere on the board
/Power stage/GDRV_RDY_TTL: U10.3; also elsewhere on the board
/Power stage/Halfbridge Driver A/GATE_H: Q2.1 (G_AH); also elsewhere on the board
/Power stage/Halfbridge Driver A/GATE_L: Q2.3 (G_AL); also elsewhere on the board
/Power stage/Halfbridge Driver A/SRC_H: Q2.2 (S_AH); also elsewhere on the board
/Power stage/Halfbridge Driver A/SRC_L: Q2.4 (S_AL); also elsewhere on the board
/Power stage/Halfbridge Driver B/GATE_H: Q2.5 (G_BH); also elsewhere on the board
/Power stage/Halfbridge Driver B/GATE_L: Q2.7 (G_BL); also elsewhere on the board
/Power stage/Halfbridge Driver B/SRC_H: Q2.6 (S_BH); also elsewhere on the board
/Power stage/Halfbridge Driver B/SRC_L: Q2.8 (S_BL); also elsewhere on the board
/Power stage/Halfbridge Driver C/GATE_H: Q2.9 (G_CH); also elsewhere on the board
/Power stage/Halfbridge Driver C/GATE_L: Q2.11 (G_CL); also elsewhere on the board
/Power stage/Halfbridge Driver C/SRC_H: Q2.10 (S_CH); also elsewhere on the board
/Power stage/Halfbridge Driver C/SRC_L: Q2.12 (S_CL); also elsewhere on the board
/Power stage/PWM_AH: U11.3 (A2); also elsewhere on the board
/Power stage/PWM_AH_TTL: U11.18 (B2), W2.1; also elsewhere on the board
/Power stage/PWM_AL: U11.4 (A3); also elsewhere on the board
/Power stage/PWM_AL_TTL: U11.17 (B3), W3.1; also elsewhere on the board
/Power stage/PWM_BH: U11.5 (A4); also elsewhere on the board
/Power stage/PWM_BH_TTL: U11.16 (B4); also elsewhere on the board
/Power stage/PWM_BL: U11.6 (A5); also elsewhere on the board
/Power stage/PWM_BL_TTL: U11.15 (B5); also elsewhere on the board
/Power stage/PWM_CH: U11.7 (A6); also elsewhere on the board
/Power stage/PWM_CH_TTL: U11.14 (B6); also elsewhere on the board
/Power stage/PWM_CL: U11.8 (A7); also elsewhere on the board
/Power stage/PWM_CL_TTL: U11.13 (B7); also elsewhere on the board
/Power stage/Y: C61.2, C62.1, MNT3.1, R56.2, R57.1
/Power stage/~FLT_DESAT_TTL: U10.1; also elsewhere on the board
/Power stage/~GDRV_RDY: U10.4; also elsewhere on the board
/Power stage/~PWR_RESET: R54.1, U11.1 (A1); also elsewhere on the board
/Power stage/~PWR_RESET_TTL: U11.20 (B1); also elsewhere on the board
BUS+: C61.1, C63.1, C64.1, C65.1, C66.1, C67.1, C68.1, C69.1, C70.1, C71.1, C72.1, C73.1, C74.1, C75.1, C76.1, C77.1, C78.1, C79.1, C80.1, C81.1, C82.1, C83.1, C84.1, C85.1, C86.1, C87.1, C88.1, C89.1, C90.1, Q2.15 (V+), Q2.16 (V+), Q2.25 (V+), Q2.26 (V+), R56.1; also elsewhere on the board
BUS-: C62.2, C63.2, C64.2, C65.2, C66.2, C67.2, C68.2, C69.2, C70.2, C71.2, C72.2, C73.2, C74.2, C75.2, C76.2, C77.2, C78.2, C79.2, C80.2, C81.2, C82.2, C83.2, C84.2, C85.2, C86.2, C87.2, C88.2, C89.2, C90.2, Q2.13 (V-), Q2.14 (V-), Q2.27 (V-), Q2.28 (V-), R57.2; also elsewhere on the board
CCS_NTC_1: Q2.18; also elsewhere on the board
CCS_NTC_2: Q2.17; also elsewhere on the board
GND: C58.2, C59.2, C60.2, R49.1, R54.2, U10.2 (GND), U11.11 (GND), U11.PAD (GND); also elsewhere on the board
unnamed: D33.1 (K), R49.2
PHASE_A: Q2.23 (PHASE_A), Q2.24 (PHASE_A); also elsewhere on the board
PHASE_B: Q2.21 (PHASE_B), Q2.22 (PHASE_B); also elsewhere on the board
PHASE_C: Q2.19 (PHASE_C), Q2.20 (PHASE_C); also elsewhere on the board

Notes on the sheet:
5V to 3.3V level conversion
3.3V to 5V level conversion
Y capacitor for heatsink
DC-link bypass caps, top side
bottom side

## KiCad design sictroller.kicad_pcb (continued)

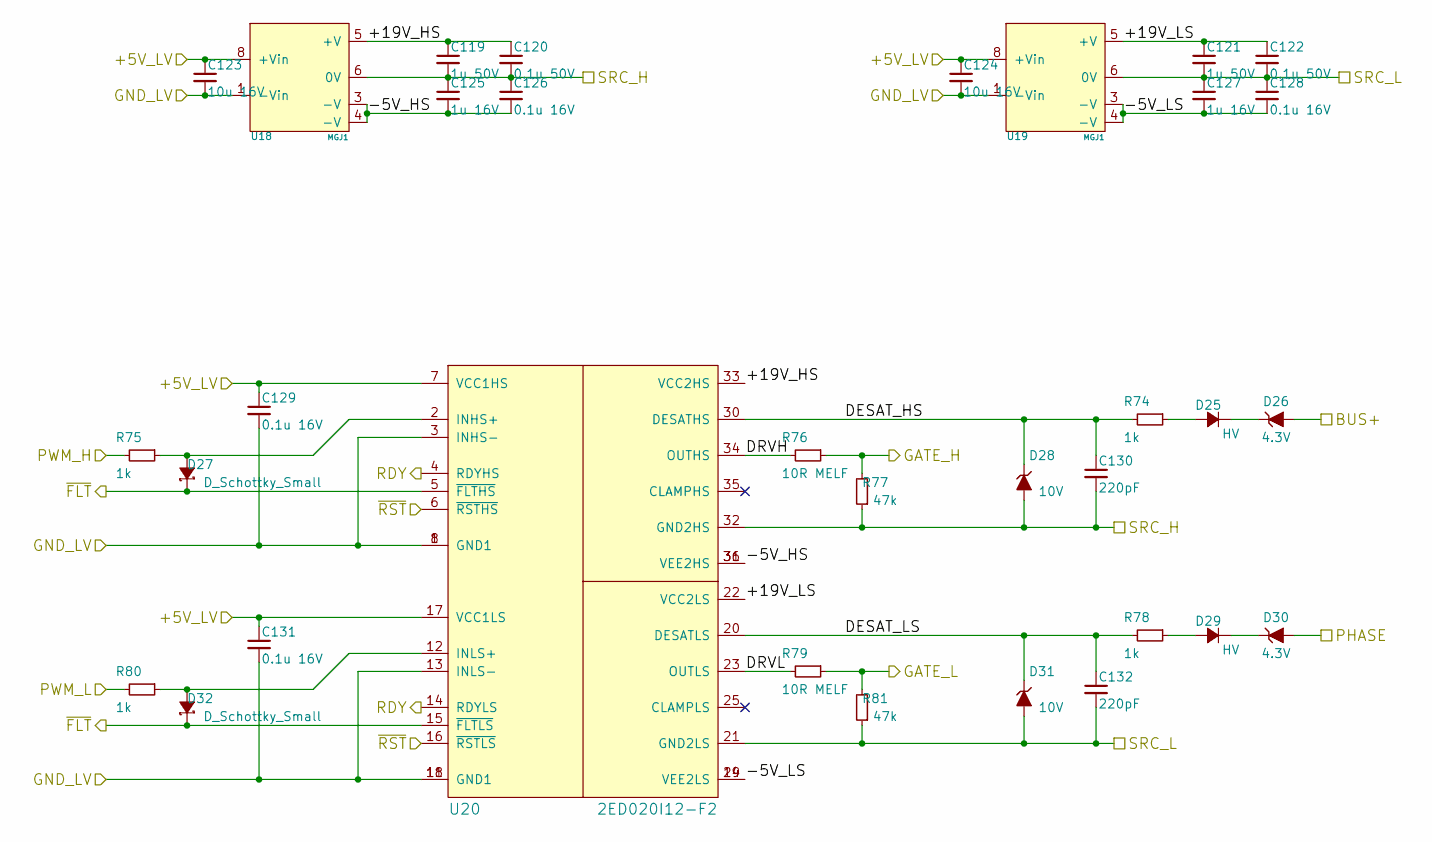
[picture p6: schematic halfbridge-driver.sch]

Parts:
C91, C93: 1u 50V; C_0805
C92, C94: 0.1u 50V; C_0603
C95, C96: 10u 16V; C_0805
C97, C99: 1u 16V; C_0603
C98, C100, C101, C103: 0.1u 16V; C_0402
C102, C104: 220pF; C_0402
D9, D13: HV; SMA_Standard
D10, D14: 4.3V; SOD-523
D11, D16: D_Schottky_Small; SOD-523
D12, D15: 10V; SOD-523
R58, R59, R62, R64: 1k; R_0402
R60, R63: 10R MELF; MELF-0204
R61, R65: 47k; R_0805
U12, U13: MGJ1
U14: 2ED020I12-F2; PG-DSO-36-58

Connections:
+5VD: C95.1, C96.1, C101.1, C103.1, U12.8 (+Vin), U13.8 (+Vin), U14.7 (VCC1HS), U14.17 (VCC1LS); also elsewhere on the board
/Power stage/GDRV_RDY_TTL: U14.4 (RDYHS), U14.14 (RDYLS); also elsewhere on the board
/Power stage/Halfbridge Driver A/+19V_HS: C91.1, C92.1, U12.5 (+V), U14.33 (VCC2HS)
/Power stage/Halfbridge Driver A/+19V_LS: C93.1, C94.1, U13.5 (+V), U14.22 (VCC2LS)
/Power stage/Halfbridge Driver A/-5V_HS: C97.2, C98.2, U12.3 (-V), U12.4 (-V), U14.31 (VEE2HS), U14.36 (VEE2HS)
/Power stage/Halfbridge Driver A/-5V_LS: C99.2, C100.2, U13.3 (-V), U13.4 (-V), U14.19 (VEE2LS), U14.24 (VEE2LS)
/Power stage/Halfbridge Driver A/DESAT_HS: C102.1, D12.1 (K), R58.2, U14.30 (DESATHS)
/Power stage/Halfbridge Driver A/DESAT_LS: C104.1, D15.1 (K), R62.2, U14.20 (DESATLS)
/Power stage/Halfbridge Driver A/DRVH: R60.2, U14.34 (OUTHS)
/Power stage/Halfbridge Driver A/DRVL: R63.2, U14.23 (OUTLS)
/Power stage/Halfbridge Driver A/GATE_H: R60.1, R61.2; also elsewhere on the board
/Power stage/Halfbridge Driver A/GATE_L: R63.1, R65.2; also elsewhere on the board
/Power stage/Halfbridge Driver A/SRC_H: C91.2, C92.2, C97.1, C98.1, C102.2, D12.2 (A), R61.1, U12.6 (0V), U14.32 (GND2HS); also elsewhere on the board
/Power stage/Halfbridge Driver A/SRC_L: C93.2, C94.2, C99.1, C100.1, C104.2, D15.2 (A), R65.1, U13.6 (0V), U14.21 (GND2LS); also elsewhere on the board
/Power stage/PWM_AH_TTL: R59.2; also elsewhere on the board
/Power stage/PWM_AL_TTL: R64.2; also elsewhere on the board
/Power stage/~FLT_DESAT_TTL: D11.1 (K), D16.1 (K), U14.5 (~FLTHS), U14.15 (~FLTLS); also elsewhere on the board
/Power stage/~PWR_RESET_TTL: U14.6 (~RSTHS), U14.16 (~RSTLS); also elsewhere on the board
BUS+: D10.2 (A); also elsewhere on the board
GND: C95.2, C96.2, C101.2, C103.2, U12.1 (-Vin), U13.1 (-Vin), U14.1 (GND1), U14.3 (INHS-), U14.8 (GND1), U14.11 (GND1), U14.13 (INLS-), U14.18 (GND1); also elsewhere on the board
unnamed: D9.2 (A), R58.1
unnamed: D9.1 (K), D10.1 (K)
unnamed: D11.2 (A), R59.1, U14.2 (INHS+)
unnamed: D13.1 (K), D14.1 (K)
unnamed: D13.2 (A), R62.1
unnamed: D16.2 (A), R64.1, U14.12 (INLS+)
PHASE_A: D14.2 (A); also elsewhere on the board

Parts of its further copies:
C105, C107, C119, C121: 1u 50V; C_0805
C106, C108, C120, C122: 0.1u 50V; C_0603
C109, C110, C123, C124: 10u 16V; C_0805
C111, C113, C125, C127: 1u 16V; C_0603
C112, C114, C115, C117, C126, C128, C129, C131: 0.1u 16V; C_0402
C116, C118, C130, C132: 220pF; C_0402
D17, D21, D25, D29: HV; SMA_Standard
D18, D22, D26, D30: 4.3V; SOD-523
D19, D24, D27, D32: D_Schottky_Small; SOD-523
D20, D23, D28, D31: 10V; SOD-523
R66, R67, R70, R72, R74, R75, R78, R80: 1k; R_0402
R68, R71, R76, R79: 10R MELF; MELF-0204
R69, R73, R77, R81: 47k; R_0805
U15, U16, U18, U19: MGJ1
U17, U20: 2ED020I12-F2; PG-DSO-36-58

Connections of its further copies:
+5VD: C109.1, C110.1, C115.1, C117.1, C123.1, C124.1, C129.1, C131.1, U15.8 (+Vin), U16.8 (+Vin), U17.7 (VCC1HS), U17.17 (VCC1LS), U18.8 (+Vin), U19.8 (+Vin), U20.7 (VCC1HS), U20.17 (VCC1LS); also elsewhere on the board
/Power stage/GDRV_RDY_TTL: U17.4 (RDYHS), U17.14 (RDYLS), U20.4 (RDYHS), U20.14 (RDYLS); also elsewhere on the board
/Power stage/Halfbridge Driver B/+19V_HS: C105.1, C106.1, U15.5 (+V), U17.33 (VCC2HS)
/Power stage/Halfbridge Driver B/+19V_LS: C107.1, C108.1, U16.5 (+V), U17.22 (VCC2LS)
/Power stage/Halfbridge Driver B/-5V_HS: C111.2, C112.2, U15.3 (-V), U15.4 (-V), U17.31 (VEE2HS), U17.36 (VEE2HS)
/Power stage/Halfbridge Driver B/-5V_LS: C113.2, C114.2, U16.3 (-V), U16.4 (-V), U17.19 (VEE2LS), U17.24 (VEE2LS)
/Power stage/Halfbridge Driver B/DESAT_HS: C116.1, D20.1 (K), R66.2, U17.30 (DESATHS)
/Power stage/Halfbridge Driver B/DESAT_LS: C118.1, D23.1 (K), R70.2, U17.20 (DESATLS)
/Power stage/Halfbridge Driver B/DRVH: R68.2, U17.34 (OUTHS)
/Power stage/Halfbridge Driver B/DRVL: R71.2, U17.23 (OUTLS)
/Power stage/Halfbridge Driver B/GATE_H: R68.1, R69.2; also elsewhere on the board
/Power stage/Halfbridge Driver B/GATE_L: R71.1, R73.2; also elsewhere on the board
/Power stage/Halfbridge Driver B/SRC_H: C105.2, C106.2, C111.1, C112.1, C116.2, D20.2 (A), R69.1, U15.6 (0V), U17.32 (GND2HS); also elsewhere on the board
/Power stage/Halfbridge Driver B/SRC_L: C107.2, C108.2, C113.1, C114.1, C118.2, D23.2 (A), R73.1, U16.6 (0V), U17.21 (GND2LS); also elsewhere on the board
/Power stage/Halfbridge Driver C/+19V_HS: C119.1, C120.1, U18.5 (+V), U20.33 (VCC2HS)
/Power stage/Halfbridge Driver C/+19V_LS: C121.1, C122.1, U19.5 (+V), U20.22 (VCC2LS)
/Power stage/Halfbridge Driver C/-5V_HS: C125.2, C126.2, U18.3 (-V), U18.4 (-V), U20.31 (VEE2HS), U20.36 (VEE2HS)
/Power stage/Halfbridge Driver C/-5V_LS: C127.2, C128.2, U19.3 (-V), U19.4 (-V), U20.19 (VEE2LS), U20.24 (VEE2LS)
/Power stage/Halfbridge Driver C/DESAT_HS: C130.1, D28.1 (K), R74.2, U20.30 (DESATHS)
/Power stage/Halfbridge Driver C/DESAT_LS: C132.1, D31.1 (K), R78.2, U20.20 (DESATLS)
/Power stage/Halfbridge Driver C/DRVH: R76.2, U20.34 (OUTHS)
/Power stage/Halfbridge Driver C/DRVL: R79.2, U20.23 (OUTLS)
/Power stage/Halfbridge Driver C/GATE_H: R76.1, R77.2; also elsewhere on the board
/Power stage/Halfbridge Driver C/GATE_L: R79.1, R81.2; also elsewhere on the board
/Power stage/Halfbridge Driver C/SRC_H: C119.2, C120.2, C125.1, C126.1, C130.2, D28.2 (A), R77.1, U18.6 (0V), U20.32 (GND2HS); also elsewhere on the board
/Power stage/Halfbridge Driver C/SRC_L: C121.2, C122.2, C127.1, C128.1, C132.2, D31.2 (A), R81.1, U19.6 (0V), U20.21 (GND2LS); also elsewhere on the board
/Power stage/PWM_BH_TTL: R67.2; also elsewhere on the board
/Power stage/PWM_BL_TTL: R72.2; also elsewhere on the board
/Power stage/PWM_CH_TTL: R75.2; also elsewhere on the board
/Power stage/PWM_CL_TTL: R80.2; also elsewhere on the board
/Power stage/~FLT_DESAT_TTL: D19.1 (K), D24.1 (K), D27.1 (K), D32.1 (K), U17.5 (~FLTHS), U17.15 (~FLTLS), U20.5 (~FLTHS), U20.15 (~FLTLS); also elsewhere on the board
/Power stage/~PWR_RESET_TTL: U17.6 (~RSTHS), U17.16 (~RSTLS), U20.6 (~RSTHS), U20.16 (~RSTLS); also elsewhere on the board
BUS+: D18.2 (A), D26.2 (A); also elsewhere on the board
GND: C109.2, C110.2, C115.2, C117.2, C123.2, C124.2, C129.2, C131.2, U15.1 (-Vin), U16.1 (-Vin), U17.1 (GND1), U17.3 (INHS-), U17.8 (GND1), U17.11 (GND1), U17.13 (INLS-), U17.18 (GND1), U18.1 (-Vin), U19.1 (-Vin), U20.1 (GND1), U20.3 (INHS-), U20.8 (GND1), U20.11 (GND1), U20.13 (INLS-), U20.18 (GND1); also elsewhere on the board
unnamed: D17.1 (K), D18.1 (K)
unnamed: D17.2 (A), R66.1
unnamed: D19.2 (A), R67.1, U17.2 (INHS+)
unnamed: D21.1 (K), D22.1 (K)
unnamed: D21.2 (A), R70.1
unnamed: D24.2 (A), R72.1, U17.12 (INLS+)
unnamed: D25.1 (K), D26.1 (K)
unnamed: D25.2 (A), R74.1
unnamed: D27.2 (A), R75.1, U20.2 (INHS+)
unnamed: D29.1 (K), D30.1 (K)
unnamed: D29.2 (A), R78.1
unnamed: D32.2 (A), R80.1, U20.12 (INLS+)
PHASE_B: D22.2 (A); also elsewhere on the board
PHASE_C: D30.2 (A); also elsewhere on the board

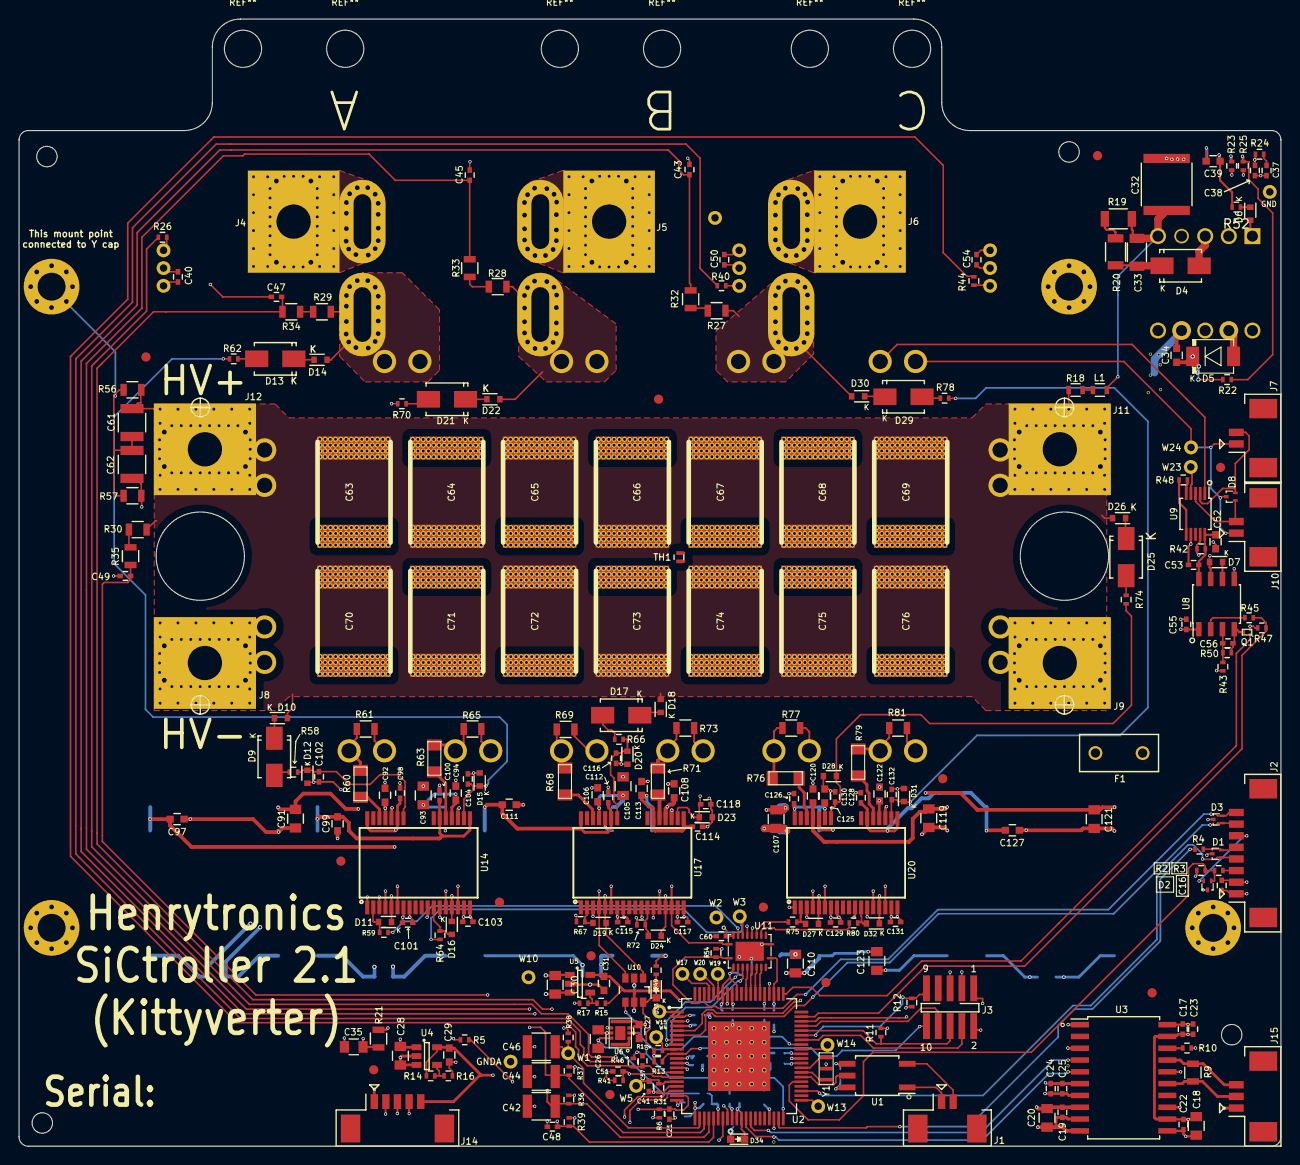
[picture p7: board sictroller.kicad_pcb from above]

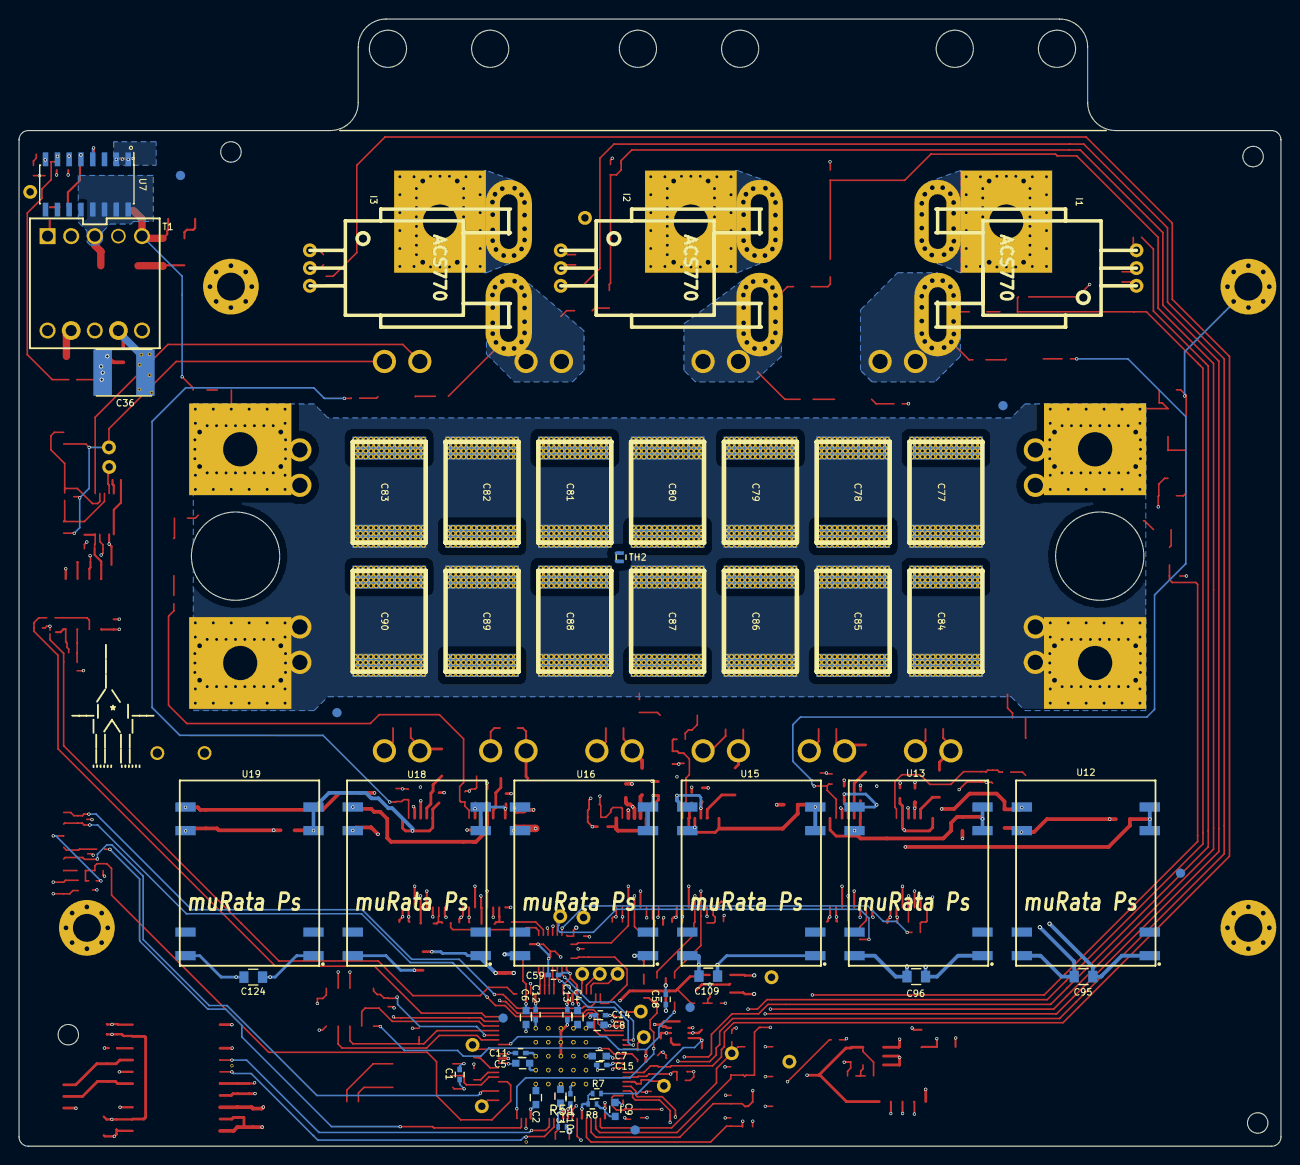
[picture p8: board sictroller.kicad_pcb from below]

Board: 6 copper layers, 135.8 x 121.3 mm, 342 parts (58 on the bottom side), 174 nets.

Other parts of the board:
GNDVIA: VIA
GNDVIA#2, GNDVIA#3, GNDVIA#4, GNDVIA#5, GNDVIA#6: VIA
MNT**: MountingHole_2.2mm_M2_DIN965
MNT**#2, MNT**#3, MNT**#4: MountingHole_2.2mm_M2_DIN965

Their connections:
GND: GNDVIA.1, GNDVIA#2.1, GNDVIA#3.1, GNDVIA#4.1, GNDVIA#5.1, GNDVIA#6.1; also elsewhere on the board

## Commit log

2016-08-03 Initial commit - symbols for ControlCard and level shifter
    [sictroller.sch]
2016-08-03 Hierarchical schematic
    [CGD15FB45P1.sch, LV_power.sch, controlcard.sch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]
2016-08-05 V0 schematic complete (?)
    [CGD15FB45P1.sch, LV_power.sch, controlcard.sch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]
2016-08-06 Annotate, fix schematic DRC, footprint for DIMM100
    [CGD15FB45P1.sch, LV_power.sch, controlcard.sch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]
2016-08-07 Footprints assigned, netlist generated - ready for layout
    [CGD15FB45P1.sch, LV_power.sch, controlcard.sch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]
2016-08-07 More aux pins, SKUs for some components
    [CGD15FB45P1.sch, LV_power.sch, controlcard.sch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]
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2016-08-07 PCB outline, mounting holes and J12/X1 placement (approx) to match CGD15FB45P1
    [sictroller.kicad_pcb]
2016-08-07 Add test points; PCB connectors placed
    [CGD15FB45P1.sch, LV_power.sch, controlcard.sch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]
2016-08-07 Change J6 (microfit) pinning for better routing of HV
    [CGD15FB45P1.sch, LV_power.sch, controlcard.sch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]
2016-08-07 Most parts placed-ish
    [sictroller.kicad_pcb]
2016-08-07 Swap level shifter pins for easier routing
    [CGD15FB45P1.sch, sictroller.kicad_pcb]
2016-08-07 About to start routing
    [sictroller.kicad_pcb]
2016-08-07 Started routing
    [sictroller.kicad_pcb]
2016-08-08 routing, but weird netnames on PWM
    [CGD15FB45P1.sch, sictroller.kicad_pcb]
2016-08-08 Fix top-level PWM miswiring
    [CGD15FB45P1.sch, sictroller.kicad_pcb, sictroller.sch]
2016-08-08 PWM and faults routed
    [sictroller.kicad_pcb, sictroller.sch]
2016-08-08 Routing progress
    [CGD15FB45P1.sch, feedback.sch, sictroller.kicad_pcb]
2016-08-08 Further routing progress
    [sictroller.kicad_pcb]
2016-08-08 routing routing
    [sictroller.kicad_pcb]
2016-08-08 Layout complete
    [sictroller.kicad_pcb, sictroller.sch]
2016-09-15 V1.0 fab output
    [sictroller-B.Cu.gbl, sictroller-B.Mask.gbs, sictroller-B.SilkS.gbo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]
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2016-09-15 Rename schematic sheets for V2
    [LV_power.sch, feedback.sch, instaspin.sch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]
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2016-10-03 schematic updates for V2; PCB draft layout
    [LV_power.sch, feedback.sch, halfbridge-driver.sch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]
2016-10-05 progress on V2 schematic
    [feedback.sch, halfbridge-driver.sch, instaspin.sch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]
2016-10-06 more v2 progress
    [LV_power.sch, feedback.sch, instaspin.sch]
2016-10-06 further V2 progress
    [LV_power.sch, instaspin.sch, sictroller.sch]
2016-10-07 V2 schem complete, footprints not assigned
    [LV_power.sch, feedback.sch, halfbridge-driver.sch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]
2016-10-07 Add TVS protection to signal I/O. Reannotate. Assign some footprints.
    [LV_power.sch, feedback.sch, halfbridge-driver.sch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]
2016-10-07 footprints assigned for instaspin and LV power
    [LV_power.sch, feedback.sch, halfbridge-driver.sch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]
2016-10-07 Footprints assigned for all except halfbridge-driver
    [feedback.sch, instaspin.sch, powerstage-CCS050M12CM2.sch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]
2016-10-07 Footprint assignment complete
    [feedback.sch, halfbridge-driver.sch, instaspin.sch]
2016-10-07 Placed SiC module, DC link caps, HV / phase terminals
    [feedback.sch, instaspin.sch, sictroller.kicad_pcb]
2016-10-07 Fix missing/duped pin assignments for 2ED020I12-F2 low-side output
2016-10-07 Place central 4 MGJ1s
    [halfbridge-driver.sch, powerstage-CCS050M12CM2.sch, sictroller.kicad_pcb]
2016-10-07 New, more boring placement of MGJ1s (vias would have been difficult)
    [sictroller.kicad_pcb]
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2016-10-07 Power stage / gate drive approx placement complete
    [halfbridge-driver.sch, sictroller.kicad_pcb]
2016-10-07 started placement of HV-LV stepdown
    [LV_power.sch, sictroller.kicad_pcb]
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2016-10-08 Add more ceralinks on rear
    [LV_power.sch, feedback.sch, halfbridge-driver.sch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]
2016-10-09 Add 1568 vias in DC link cap pads
    [LV_power.sch, feedback.sch, halfbridge-driver.sch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]
2016-10-11 Improved footprint for B6A-PCB
    [feedback.sch, halfbridge-driver.sch, powerstage-CCS050M12CM2.sch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]
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2016-10-11 Zones for phase connections
    [sictroller.kicad_pcb]
2016-10-11 Zones for phase connections 2
    [sictroller.kicad_pcb]
2016-10-11 Zones for phase connections 3
    [sictroller.kicad_pcb]
2016-10-11 Swap PWM nets on 28069M for easier routing
    [instaspin.sch, sictroller.kicad_pcb]
2016-10-11 Add aux connector for vibe monitor
    [LV_power.sch, feedback.sch, halfbridge-driver.sch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]
2016-10-12 some logic placement progress
    [LV_power.sch, feedback.sch, halfbridge-driver.sch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]
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2016-10-18 routed underside of 28069M
    [sictroller.kicad_pcb]
2016-10-18 Route CAN isolated section
    [instaspin.sch, sictroller.kicad_pcb]
2016-10-18 most planes in place
    [sictroller.kicad_pcb]
2016-10-18 gate drive source planes in place
    [sictroller.kicad_pcb]
2016-10-19 routing progress - gate driver LV sides complete
    [sictroller.kicad_pcb]
2016-10-19 3.3V and 1.8V supplies routed; fixed wrong connections on 1.8V regulator
    [LV_power.sch, halfbridge-driver.sch, instaspin.sch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]
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2016-10-20 further routing; add fault LED
    [powerstage-CCS050M12CM2.sch, sictroller.kicad_pcb]
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2016-10-20 the end is in sight
    [feedback.sch, halfbridge-driver.sch, sictroller.kicad_pcb]
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2016-10-21 DRC pass (haven't checked 9/9 on inner layers)
    [sictroller.kicad_pcb]
2016-10-21 inner layer 9/9 visually checked; starting silkscreen
    [sictroller.kicad_pcb]
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2016-10-21 silkscreen complete top side?
    [sictroller.kicad_pcb]
2016-10-21 Silkscreen done both sides, added aux LED
    [LV_power.sch, feedback.sch, instaspin.sch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]
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2016-10-21 Add M2 mounting holes for cover
    [feedback.sch, halfbridge-driver.sch, sictroller.kicad_pcb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]
2016-10-21 As sent to Tempo 2016-10-21
    [LV_power.sch, feedback.sch, halfbridge-driver.sch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]
2016-10-28 Minor fixups from Tempo DFM
    [sictroller.kicad_pcb]
2016-12-03 Errata from v2.0 bringup
    [TA_bom_sictroller_v2_rev0.xlsx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]
2016-12-03 V2.1: Fixes for V2.0 bugs
    [LV_power.sch, halfbridge-driver.sch, instaspin.sch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]
2017-12-25 errata updates and schematic comments
    [LV_power.sch, feedback.sch, halfbridge-driver.sch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]
